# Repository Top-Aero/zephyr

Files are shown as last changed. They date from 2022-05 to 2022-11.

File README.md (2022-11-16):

# Zéphyr

forthebadge  

---

## Description

Le vent d'Ouest, fils d'Astreos et d'Éos, attise le feu de notre inspiration : Zéphyr. Projet phare de l'association [Top Aéro](https://www.top-aero.com/), il s'agit d'une fusée expérimentale transsonique dont la coiffe est équipée de capteurs de pression, afin d'observer l'écoulement de l'air qui l'entoure, puis d'en comparer les résultats à une simulation numérique faite préalablement.

Le dépôt Git contient les conceptions des PCB du système électronique et les codes des microcontrôleurs contenus dans la case électronique de la fusée. Ils sont respectivement contenus dans `case_elec` et `code`.

### Structure du dossier `case_elec`

```
case_elec
├───odb
│   └───odb-backups
├───ressources
└───seq
    └───seq-backups
```

Les sous-dossiers odb et seq, désignant respectivement l'ordinateur de bord et le séquenceur embarqués dans la fusée, contiennent des projets KiCAD, le logiciel de CAO pour l'électronique qui a été utilisé durant la phase de conception. Les fichiers de conception, d'extension kicad_pro, kicad_sch et kicad_pcb suffisent à décrire ce qui a été conçu, mais le fichier .gitignore que nous avions rédigé (il sert à filtrer les documents inutiles dans le workflow Git) a été insuffisant. Avec le temps et le ménage qui n'est pas fait, des documents supplémentaires finissent par encombrer les dossiers KiCAD. Il est tout de même intéressant de les décrire :

- les `*.gbr` sont les fichiers de fabrication, générés par le logiciel ;
- les `*.step` sont les fichiers de visualisation 3D de la carte électronique et des composants ;
- les dossiers `*-backups` contiennent les versions précédentes au format zip d'un même projet.

Les -backups se sont avérés vitaux à une ou deux reprises lorsque nous supprimions des éléments critiques par inadvertance. Bien qu'inutiles en soi, ils compensaient le manque de maîtrise que l'on avait de Git et de KiCAD et faisaient gagner beaucoup de temps. À l'avenir, il faudra penser à configurer KiCAD pour ne conserver que la dernière version, car c'est la plus utile en cas de pépin.

#### Structure du dossier `ressources`

```
ressources
├───3Dmodels
│   └───teensy
├───lib_fp
│   ├───Adafruit BNO055
│   │   ├───Adafruit BNO055-backups
│   │   └───Adafruit BNO055.pretty
│   ├───Adafruit Ultimate GPS
│   │   └───Adafruit Ultimate GPS-backups
│   ├───Adafruit_sensors.pretty
│   ├───Adafruit_Ultimate_GPS
│   │   ├───Adafruit_Ultimate_GPS-backups
│   │   └───Adafruit_Ultimate_GPS.pretty
│   ├───common_misc.pretty
│   ├───MPL3115A2_v0.2
│   │   ├───MPL3115A2_v0.2-backups
│   │   └───MPL3115A2_v0.2.pretty
│   ├───Reyax.pretty
│   └───teensy.pretty
├───lib_sch
└───tmp_resources
    ├───Adafruit-BNO055-Breakout-PCB-master
    │   └───assets
    ├───Adafruit-MPL3115A2-PCB-master
    │   └───assets
    ├───prj
    │   └───altimetre
    └───zip
```

Le dossier ressources se structure ainsi :

- 3Dmodels : contient les modèles 3D des composants. Utile pour la visualisation et l'export au format .step ;
- lib_fp : *library footprints*, contient les empreintes des composants utilisés, c'est-à-dire leur contour et les trous à placer sur la carte électronique ;
- lib_sch : *library schematics*, contient les symboles électriques utilisés dans les schémas électriques ;
- liensUtiles.txt : contient des liens vers des bibliothèques d'empreintes, de symboles électriques et de modèles 3D.
- tmp_ressources : un dossier un peu fouillis qu'il faudrait prendre le temps de réhabiliter.

Le fichier liensUtiles.txt porte mal son nom, car les sites vers lesquels il renvoie se sont avéré moins utiles qu'espérés : des composants complexes comme les capteurs Adafruit n'y sont pas documentés. Il a fallu, et il a mieux valu concevoir par nous même les empreintes, même approximativement. Par ailleurs, Adafruit met à disposition des modèles 3D de leurs composants sur [cette page GitHub](https://github.com/adafruit/Adafruit_CAD_Parts). Toutes les entreprises n'en font pas autant.

### Structure du dossier `code`

```
code
├───seq
├───station-sol
└───telemetrie
    ├───TopAeroEM
    ├───TopAeroEM0720
    ├───TopAeroEM_test_pitot
    └───TopAeroRV
```

Les dossiers seq, TopAEroEM (EM pour émission) et TopAéroRV (RV pour récéption...) dans telemetrie contiennent des fichiers ino. C'est le format de fichier que reconnaît l'éditeur Arduino que l'on utilisait pour programmer les microcontrôleurs de la case électronique. Pour plusieurs raisons, il faut lui préférer à l'avenir son alternative PlatfomIO soit en tant qu'extension, soit en standalone à intégrer au workflow de votre IDE de choix. Pour les experts, un makefile Arduino peut suffire.

Plusieurs dossiers TopAeroEM se côtoient. Une convention de nommage récurrente est de suffixer à une autre version d'un même dossier le mois puis le jour où cette version a vu le jour, en quatre chiffres. Ainsi, le dossier TopAeroEM0720 est une version de TopAeroEM créée un 20 juillet. Des exceptions subsistent (TopAeroEM_test_pitot), mais tant qu'elles ne sont pas nombreuses (plus que 2), elles restent gérables. Ces deux pratiques sont tout de même à éviter, car elles ne tirent pas profit de la technologie de versionnage de Git. Il faut préférer mettre à jour le code existant, ou encore ajouter une nouvelle branche au projet, ou dans le pire des cas, se passer complètement du workflow Git si le contraire amenait à désorganiser la structure du projet.

Le dossier station-sol contient plusieurs scripts qui n'ont pas pu être déployés. Le seul script utilisable en l'état est simpleUSBlogger.py qui se charge d'écrire dans un fichier les données réceptionnées.

## Derniers mots

La fusée a décollé un jour de juillet 2022. À part quelque modifications mineures et sporadiques sur sa page GitHub, le projet est terminé.

## Contacts

Nom               | Rôle                              | Contact
------------------|-----------------------------------|----------
Mohamed-Iadh Bani | Conception séquenceur             | [:e-mail:](mailto:mohamed-iadh.bani@top-aero.com) [:octocat:](https://github.com/mediadhBani)
Théo Tugayé       | Conception ordinateur de bord     | [:e-mail:](mailto:theo.tugaye@top-aero.com) [:octocat:](https://github.com/Alhucarr)

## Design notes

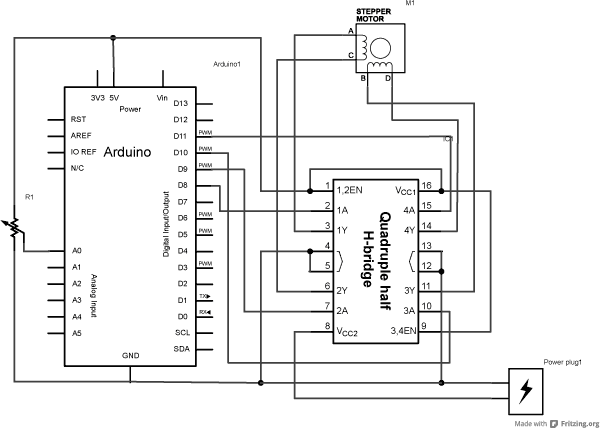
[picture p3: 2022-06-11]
code/stepper/schema_stepper+quadrupleDemiPontH.png

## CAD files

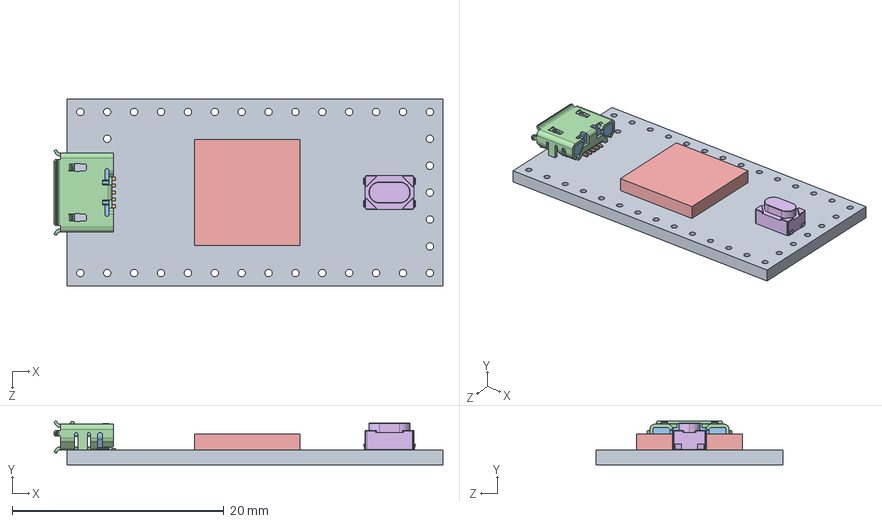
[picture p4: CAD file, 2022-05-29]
case_elec/ressources/3Dmodels/teensy/Teensy_4.0_Assembly.STEP
36.8 x 4.12 x 17.7 mm
Teensy_4.0_PCB
Micro USB-B Female 5Pin SMD
NXP iMXRT1062
SKRPACE010 v4

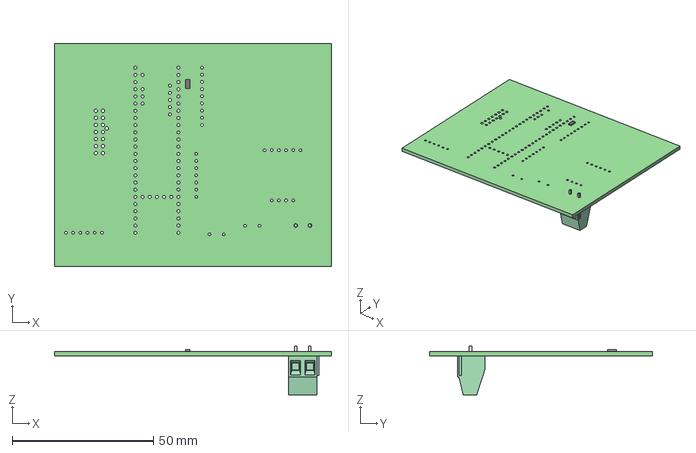
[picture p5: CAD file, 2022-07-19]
case_elec/odb/odb.step
98.0 x 79.0 x 17.3 mm
odb PCB

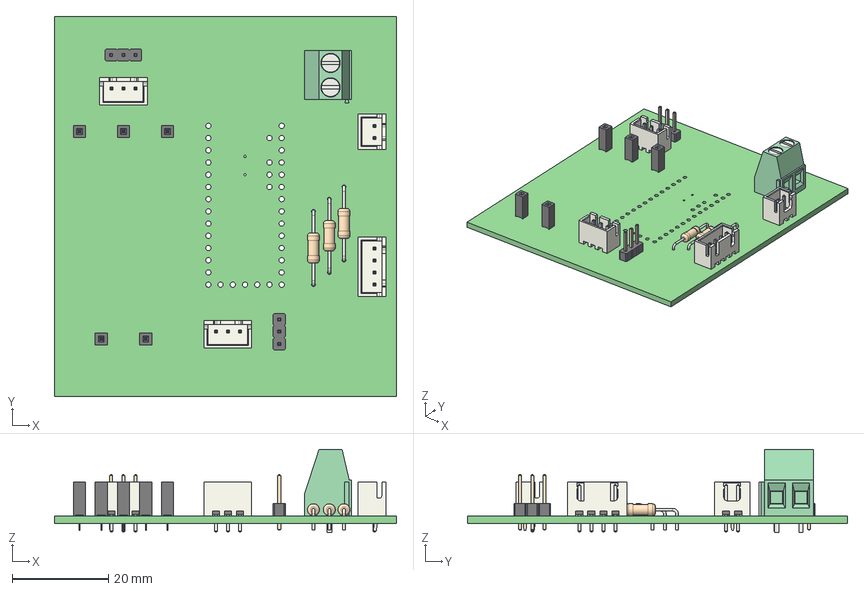
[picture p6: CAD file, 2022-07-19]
case_elec/seq/seq.step
71.1 x 79.0 x 17.3 mm
_autosave-seq PCB

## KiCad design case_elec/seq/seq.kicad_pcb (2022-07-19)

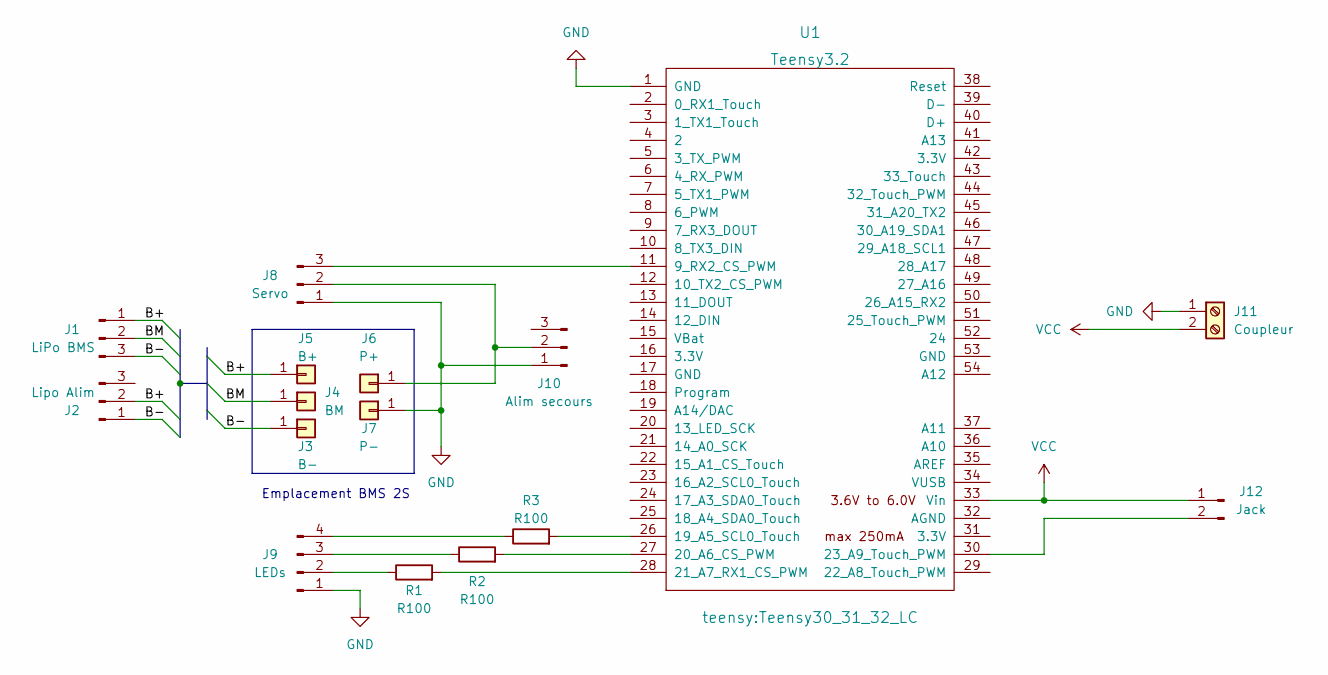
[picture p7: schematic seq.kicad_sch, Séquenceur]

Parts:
J1: LiPo BMS; JST_XH_B3B-XH-A_1x03_P2.50mm_Vertical
J2: Lipo Alim; PinHeader_1x03_P2.54mm_Vertical
J3: B+; PinSocket_1x01_P2.54mm_Vertical
J4: BM; PinSocket_1x01_P2.54mm_Vertical
J5: B-; PinSocket_1x01_P2.54mm_Vertical
J6: P+; PinSocket_1x01_P2.54mm_Vertical
J7: P-; PinSocket_1x01_P2.54mm_Vertical
J8: Servo; JST_XH_B3B-XH-A_1x03_P2.50mm_Vertical
J9: LEDs; JST_XH_B4B-XH-A_1x04_P2.50mm_Vertical
J10: Alim secours; PinHeader_1x03_P2.54mm_Vertical
J11: Coupleur; TerminalBlock_Phoenix_MKDS-1,5-2-5.08_1x02_P5.08mm_Horizont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
J12: Jack; JST_XH_B2B-XH-A_1x02_P2.50mm_Vertical
R1, R2, R3: R100; R_Axial_DIN0207_L6.3mm_D2.5mm_P15.24mm_Horizontal
U1: Teensy3.2; Teensy30_31_32_LC

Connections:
/B+: J1.1, J2.2, J3.1
/B-: J1.3, J2.1, J5.1
/BM: J1.2, J4.1
GND: J7.1, J8.1, J9.1, J10.1, J11.1, U1.1 (GND)
unnamed: J8.3, U1.11 (9_RX2_CS_PWM)
unnamed: J9.2, R1.1
unnamed: J9.3, R2.1
unnamed: J9.4, R3.1
unnamed: J6.1, J8.2, J10.2
unnamed: J12.2, U1.30 (23_A9_Touch_PWM)
unnamed: R1.2, U1.28 (21_A7_RX1_CS_PWM)
unnamed: R2.2, U1.27 (20_A6_CS_PWM)
unnamed: R3.2, U1.26 (19_A5_SCL0_Touch)
VCC: J11.2, J12.1, U1.33 (Vin)

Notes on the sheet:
Emplacement BMS 2S

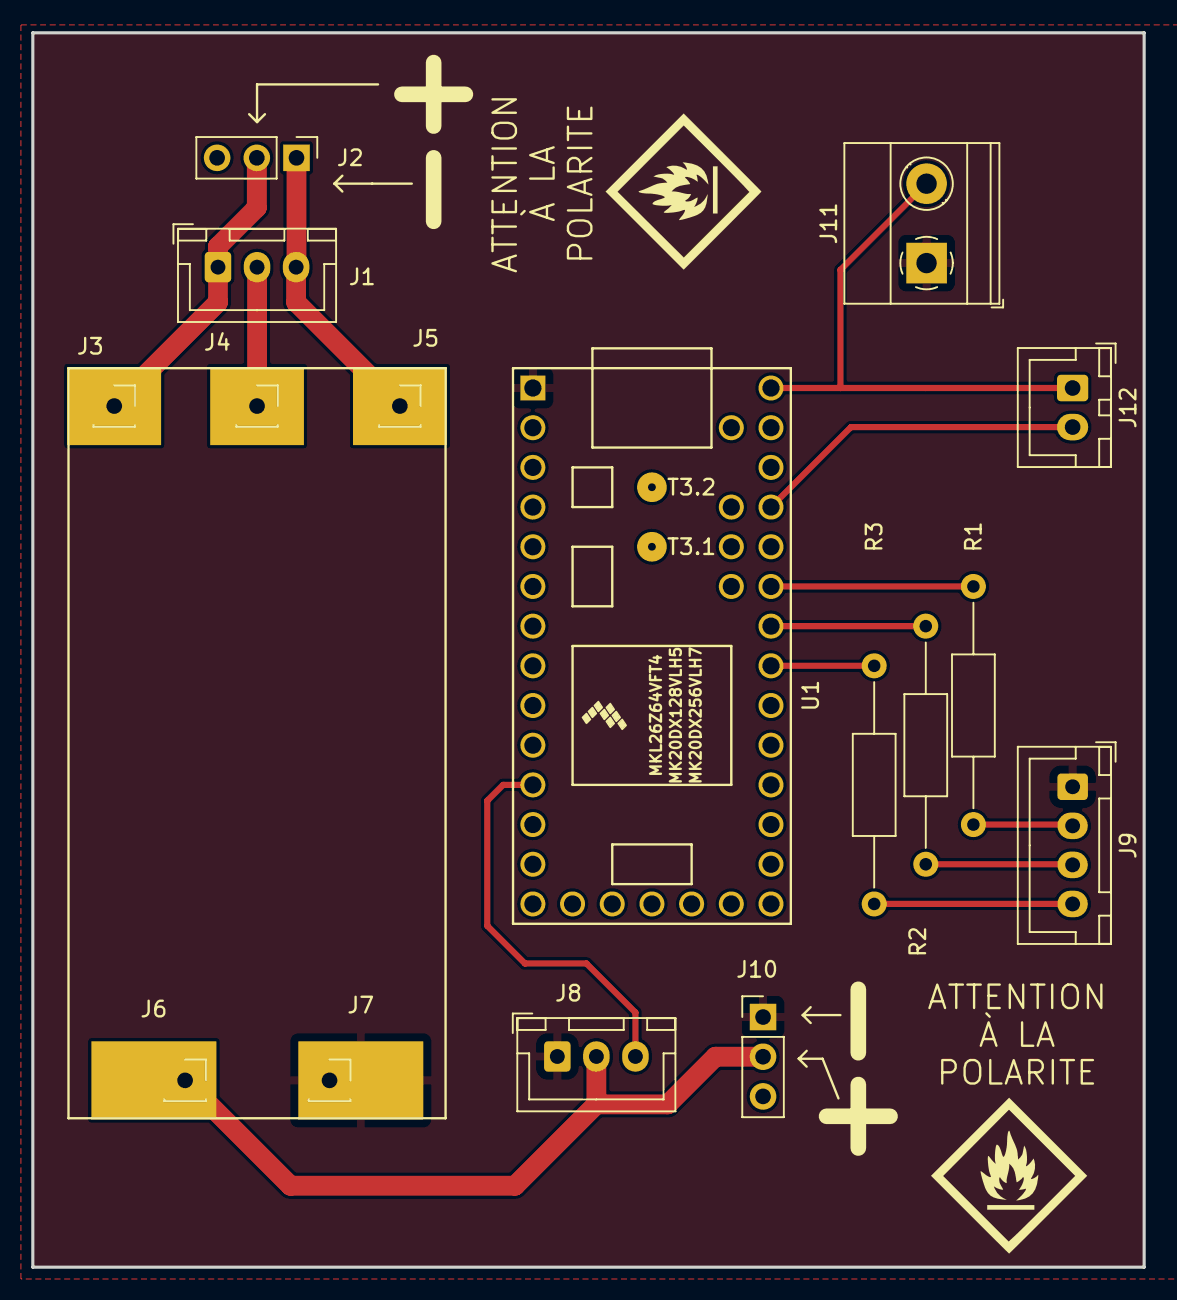
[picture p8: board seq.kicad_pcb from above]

Board: 2 copper layers, 71.1 x 79.0 mm, 16 parts (0 on the bottom side), 14 nets.

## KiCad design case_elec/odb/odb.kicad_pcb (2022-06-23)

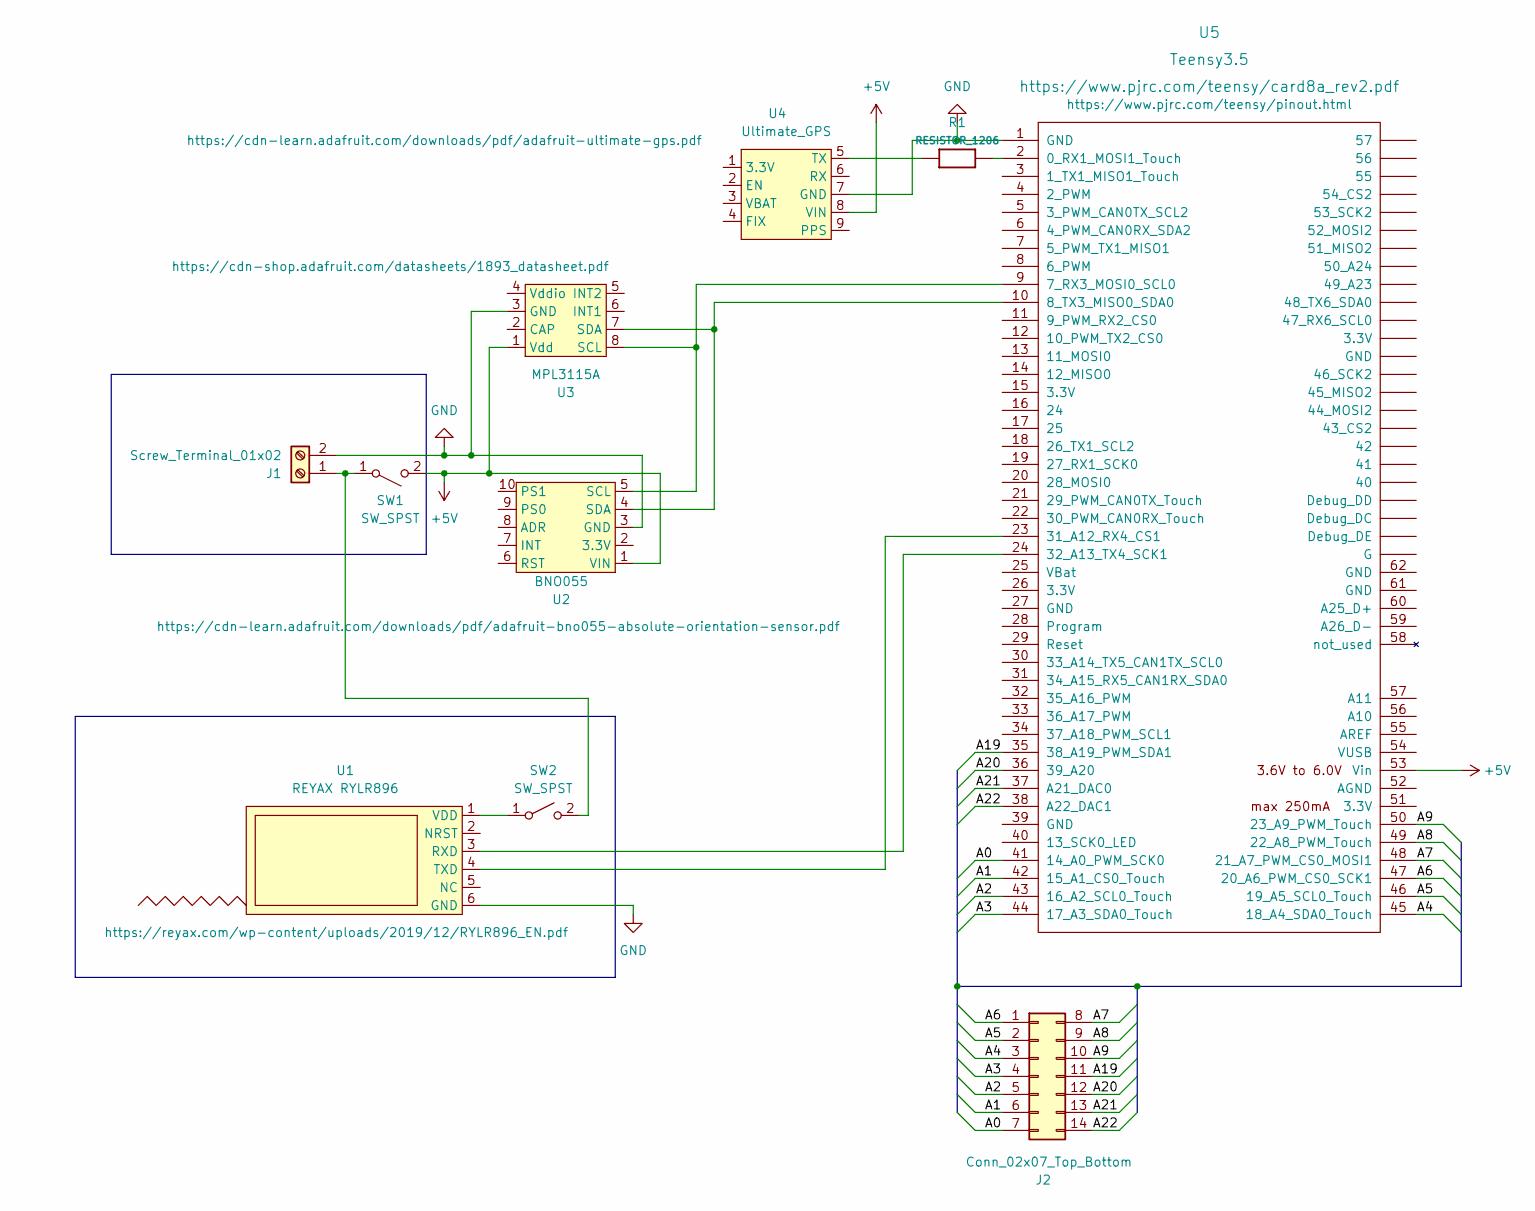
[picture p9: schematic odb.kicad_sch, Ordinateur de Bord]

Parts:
J1: Screw_Terminal_01x02; TerminalBlock_Phoenix_MKDS-1,5-2-5.08_1x02_P5.08mm_Horizont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
J2: Conn_02x07_Top_Bottom; Molex_Nano-Fit_105310-xx14_2x07_P2.50mm_Vertical
R1: RESISTOR_1206; R_1206_3216Metric_Pad1.30x1.75mm_HandSolder
SW1, SW2: SW_SPST; SW
U1: REYAX RYLR896; RYLR896
U2: BNO055
U3: MPL3115A; MPL3115A2
U4: Ultimate_GPS
U5: Teensy3.5; Teensy35_36

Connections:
+5V: SW1.2 (B), U2.1 (VIN), U3.1 (Vdd), U4.8 (VIN), U5.53 (Vin)
/A0: J2.7, U5.41 (14_A0_PWM_SCK0)
/A1: J2.6, U5.42 (15_A1_CS0_Touch)
/A2: J2.5, U5.43 (16_A2_SCL0_Touch)
/A3: J2.4, U5.44 (17_A3_SDA0_Touch)
/A4: J2.3, U5.45 (18_A4_SDA0_Touch)
/A5: J2.2, U5.46 (19_A5_SCL0_Touch)
/A6: J2.1, U5.47 (20_A6_PWM_CS0_SCK1)
/A7: J2.8, U5.48 (21_A7_PWM_CS0_MOSI1)
/A8: J2.9, U5.49 (22_A8_PWM_Touch)
/A9: J2.10, U5.50 (23_A9_PWM_Touch)
/A19: J2.11, U5.35 (38_A19_PWM_SDA1)
/A20: J2.12, U5.36 (39_A20)
/A21: J2.13, U5.37 (A21_DAC0)
/A22: J2.14, U5.38 (A22_DAC1)
GND: J1.2, U1.6 (GND), U2.3 (GND), U3.3 (GND), U4.7 (GND), U5.1 (GND)
unnamed: J1.1, SW1.1 (A), SW2.2 (B)
unnamed: SW2.1 (A), U1.1 (VDD)
unnamed: U1.3 (RXD), U5.24 (32_A13_TX4_SCK1)
unnamed: U1.4 (TXD), U5.23 (31_A12_RX4_CS1)
unnamed: U2.4 (SDA), U3.7 (SDA), U5.10 (8_TX3_MISO0_SDA0)
unnamed: U2.5 (SCL), U3.8 (SCL), U5.9 (7_RX3_MOSI0_SCL0)
unnamed: R1.1, U4.5 (TX)
unnamed: R1.2, U5.2 (0_RX1_MOSI1_Touch)

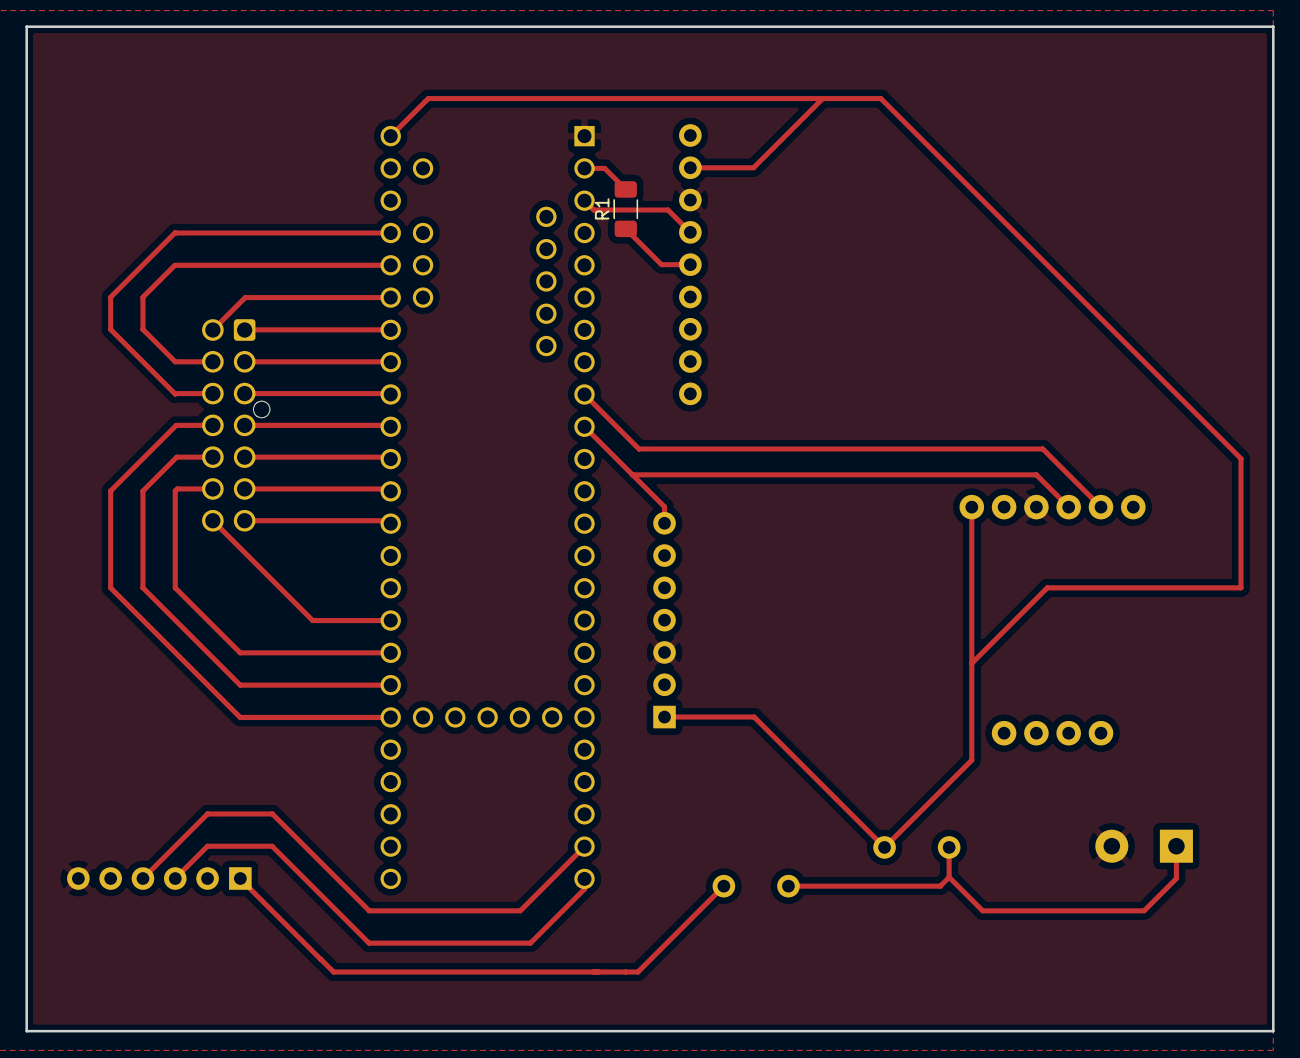
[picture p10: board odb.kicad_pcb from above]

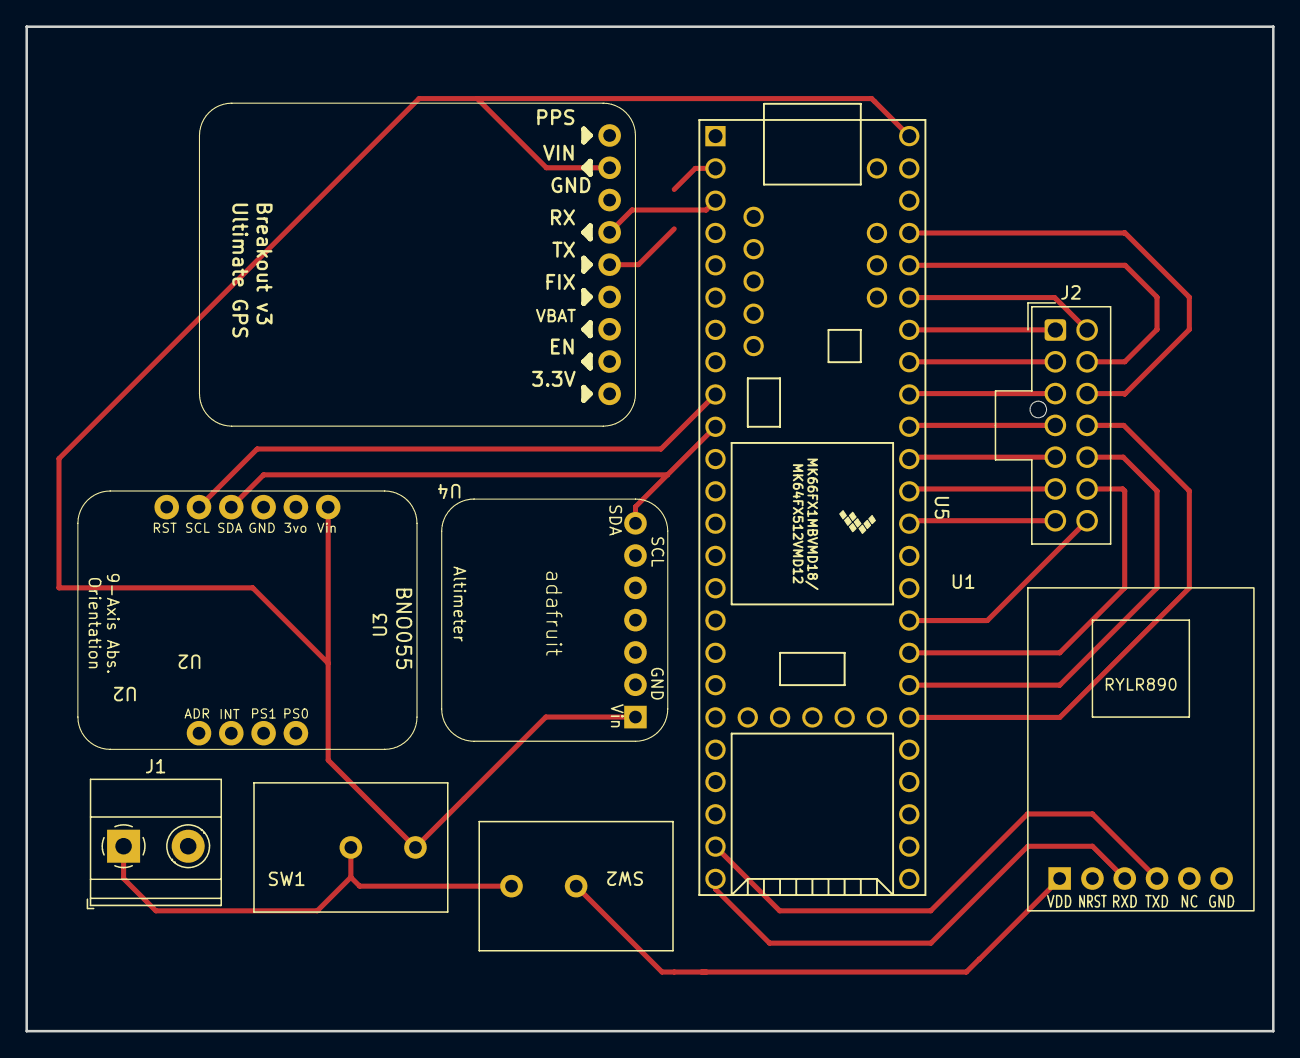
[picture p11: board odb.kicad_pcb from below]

Board: 2 copper layers, 98.0 x 79.0 mm, 10 parts (9 on the bottom side), 24 nets.

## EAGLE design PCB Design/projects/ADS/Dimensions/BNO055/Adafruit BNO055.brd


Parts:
C1, C2: 22pF; 0805-NO
C3: 0.1uF; 0805-NO
C4: 0.1uF; 0805_10MGAP
C5: 10uF; 0805-NO
C6: 10uF; 0805_10MGAP
D1: 1n4148; SOD-323
FID1, FID2: FIDUCIAL""; FIDUCIAL_1MM
JP1: HEADER-1X676MIL; 1X06_ROUND_76
JP2: HEADER-1X476MIL; 1X04_ROUND_76
Q1, Q2: BSS138; SOT23-WIDE
R3, R4, R5, R6, R7, R10: 10K; 0805-NO
R8, R9: 10K; _0805MP
U1: MIC5225-3.3; SOT23-5
U$2: BNO055
U$29, U$30, U$31, U$32: MOUNTINGHOLE2.5_THICK; MOUNTINGHOLE_2.5_PLATED_THICK
Y1: 32.768kHz; CRYSTAL_8X3.8

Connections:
3.3V: C4.2, C6.1, JP1.2, Q1.1 (G), Q2.1 (G), R6.2, R7.2, R10.2, U1.5 (OUT), U$2.3 (VDD), U$2.4 (NBOOT_LOAD_PIN), U$2.28 (VDDIO)
5.0V: C5.1, JP1.1, R8.2, R9.2, U1.1 (IN), U1.3 (EN)
GND: C1.1, C2.1, C3.1, C4.1, C5.2, C6.2, JP1.3, R3.2, R4.2, R5.2, U1.2 (GND), U$2.2 (GND), U$2.10 (PIN10(GND)), U$2.15 (PIN15(GND)), U$2.16 (PIN16(GND)), U$2.18 (COM2(GND)), U$2.25 (GND)
I2CADDR_3V: JP2.4, R5.1, U$2.17 (COM3/I2C_ADDR)
INT_3V: JP2.3, U$2.14 (INT)
unnamed: C1.2, U$2.27 (XIN32), Y1.P$4 (2)
unnamed: C2.2, U$2.26 (XOUT32), Y1.P$1 (1)
unnamed: C3.2, U$2.9 (CAP)
NRESET_3V: D1.A, R10.1, U$2.11 (NRESET)
PS0_3V: JP2.1, R3.1, U$2.6 (PS0)
PS1_3V: JP2.2, R4.1, U$2.5 (PS1)
RST_5V: D1.C, JP1.6
SCL_3V: Q2.2 (S), R7.1, U$2.19 (COM1/SCL/RX)
SCL_5V: JP1.5, Q2.3 (D), R9.1
SDA_3V: Q1.2 (S), R6.1, U$2.20 (COM0/SDA/TX)
SDA_5V: JP1.4, Q1.3 (D), R8.1



Board: 2 copper layers, 26.7 x 20.3 mm, 31 parts (2 on the bottom side), 16 nets.

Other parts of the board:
U$3: PCBFEAT-REV-040
U$28: ADAFRUIT_TEXT_20MM
U$33: ADAFRUIT_2.5MM

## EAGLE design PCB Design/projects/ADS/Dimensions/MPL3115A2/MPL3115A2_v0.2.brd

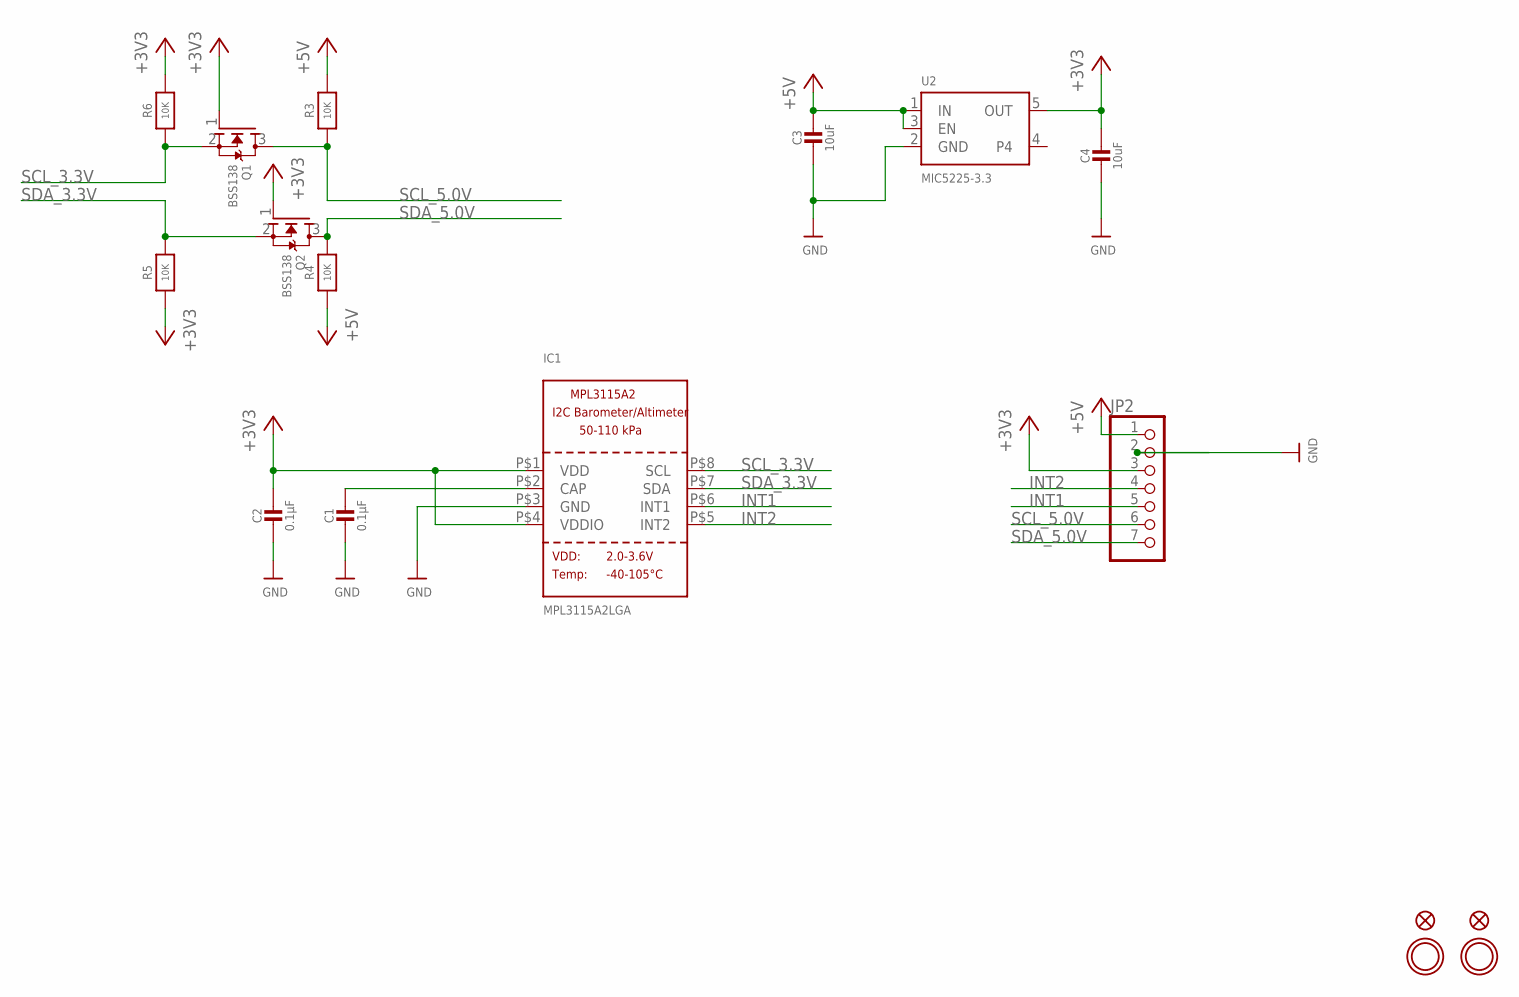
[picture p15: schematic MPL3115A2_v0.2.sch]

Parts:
C1, C2: 0.1µF; 0805-NO
C3, C4: 10uF; 0805-NO
FID1, FID2: FIDUCIAL""; FIDUCIAL_1MM
IC1: MPL3115A2LGA; LGA8
JP2: HEADER-1X770MIL; 1X07_ROUND_70
Q1, Q2: BSS138; SOT23-WIDE
R3, R4, R5, R6: 10K; 0805-NO
U2: MIC5225-3.3; SOT23-5
U$8, U$9: MOUNTINGHOLE2.5; MOUNTINGHOLE_2.5_PLATED

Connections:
+3V3: C2.1, C4.1, IC1.P$1 (VDD), IC1.P$4 (VDDIO), JP2.3, Q1.1 (G), Q2.1 (G), R5.1, R6.2, U2.5 (OUT)
+5V: C3.1, JP2.1, R3.2, R4.1, U2.1 (IN), U2.3 (EN)
CAP: C1.1, IC1.P$2 (CAP)
GND: C1.2, C2.2, C3.2, C4.2, IC1.P$3 (GND), JP2.2, U2.2 (GND)
INT1: IC1.P$6 (INT1), JP2.5
INT2: IC1.P$5 (INT2), JP2.4
SCL_3.3V: IC1.P$8 (SCL), Q1.2 (S), R6.1
SCL_5.0V: JP2.6, Q1.3 (D), R3.1
SDA_3.3V: IC1.P$7 (SDA), Q2.2 (S), R5.2
SDA_5.0V: JP2.7, Q2.3 (D), R4.2

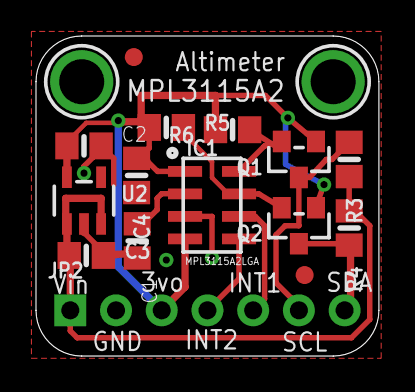
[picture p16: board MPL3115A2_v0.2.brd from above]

Board: 2 copper layers, 19.1 x 17.8 mm, 18 parts (1 on the bottom side), 10 nets.

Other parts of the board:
U$14: ADAFRUIT_3.5MM

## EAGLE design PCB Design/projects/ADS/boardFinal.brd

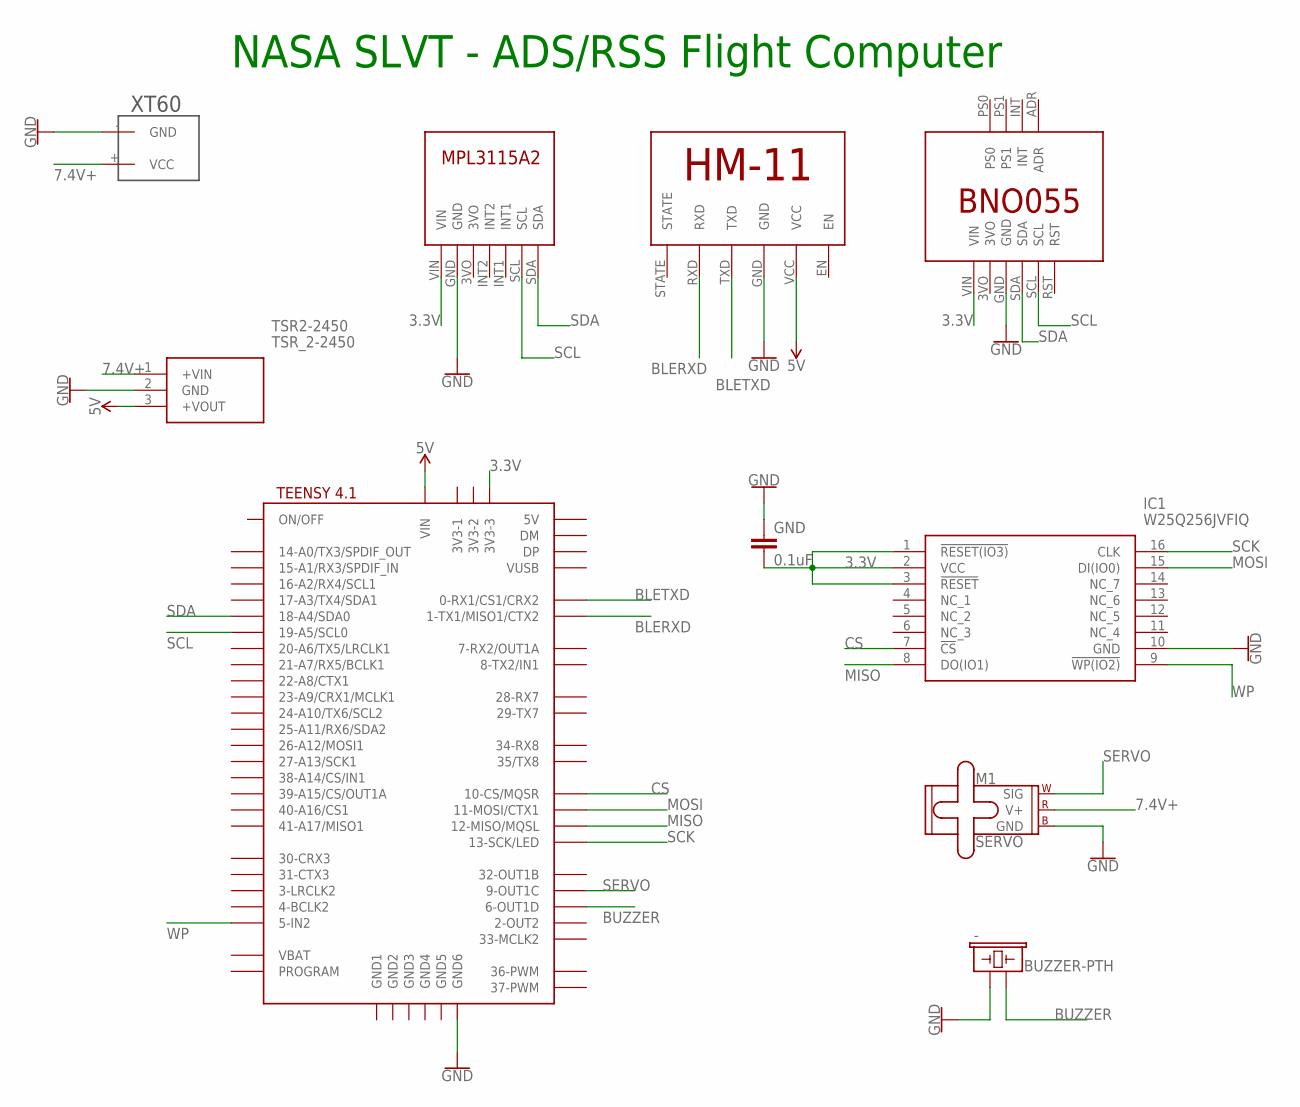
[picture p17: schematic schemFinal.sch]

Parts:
-: BUZZER-PTH; BUZZER-12MM
GND: 0.1uF; CAP-PTH-2.54
IC1: W25Q256JVFIQ; SOIC127P1032X264-16N
M1: SERVO; 1X03
TSR2-2450: TSR_2-2450; TSR-2
U$1: BNO055
U$2: MPL3115A2
U$3: TEENSY41-E; TENNSY41-E
U$4: HM-11
U$5: XT60

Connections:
3.3V: GND.2, IC1.1 (!RESET(IO3)), IC1.2 (VCC), IC1.3 (!RESET), U$1.VIN, U$2.VIN, U$3.3V3-3
5V: TSR2-2450.3 (+VOUT), U$3.VIN, U$4.VCC
7.4V+: M1.2 (V+), TSR2-2450.1 (+VIN), U$5.+ (VCC)
BLERXD: U$3.1-TX1/MISO1/CTX2, U$4.RXD
BLETXD: U$3.0-RX1/CS1/CRX2, U$4.TXD
BUZZER: -.- (2), U$3.6-OUT1D
CS: IC1.7 (!CS), U$3.10-CS\MQSR (10-CS/MQSR)
GND: -.+ (1), GND.1, IC1.10 (GND), M1.3 (GND), TSR2-2450.2 (GND), U$1.GND, U$2.GND, U$3.GND6, U$4.GND, U$5.- (GND)
MISO: IC1.8 (DO(IO1)), U$3.12-MISO/MQSL
MOSI: IC1.15 (DI(IO0)), U$3.11-MOSI/CTX1
SCK: IC1.16 (CLK), U$3.13-SCK/LED
SCL: U$1.SCL, U$2.SCL, U$3.19-A5/SCL0
SDA: U$1.SDA, U$2.SDA, U$3.18-A4/SDA0
SERVO: M1.1 (SIG), U$3.9-OUT1C
WP: IC1.9 (!WP(IO2)), U$3.5-IN2

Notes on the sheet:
NASA SLVT - ADS/RSS Flight Computer

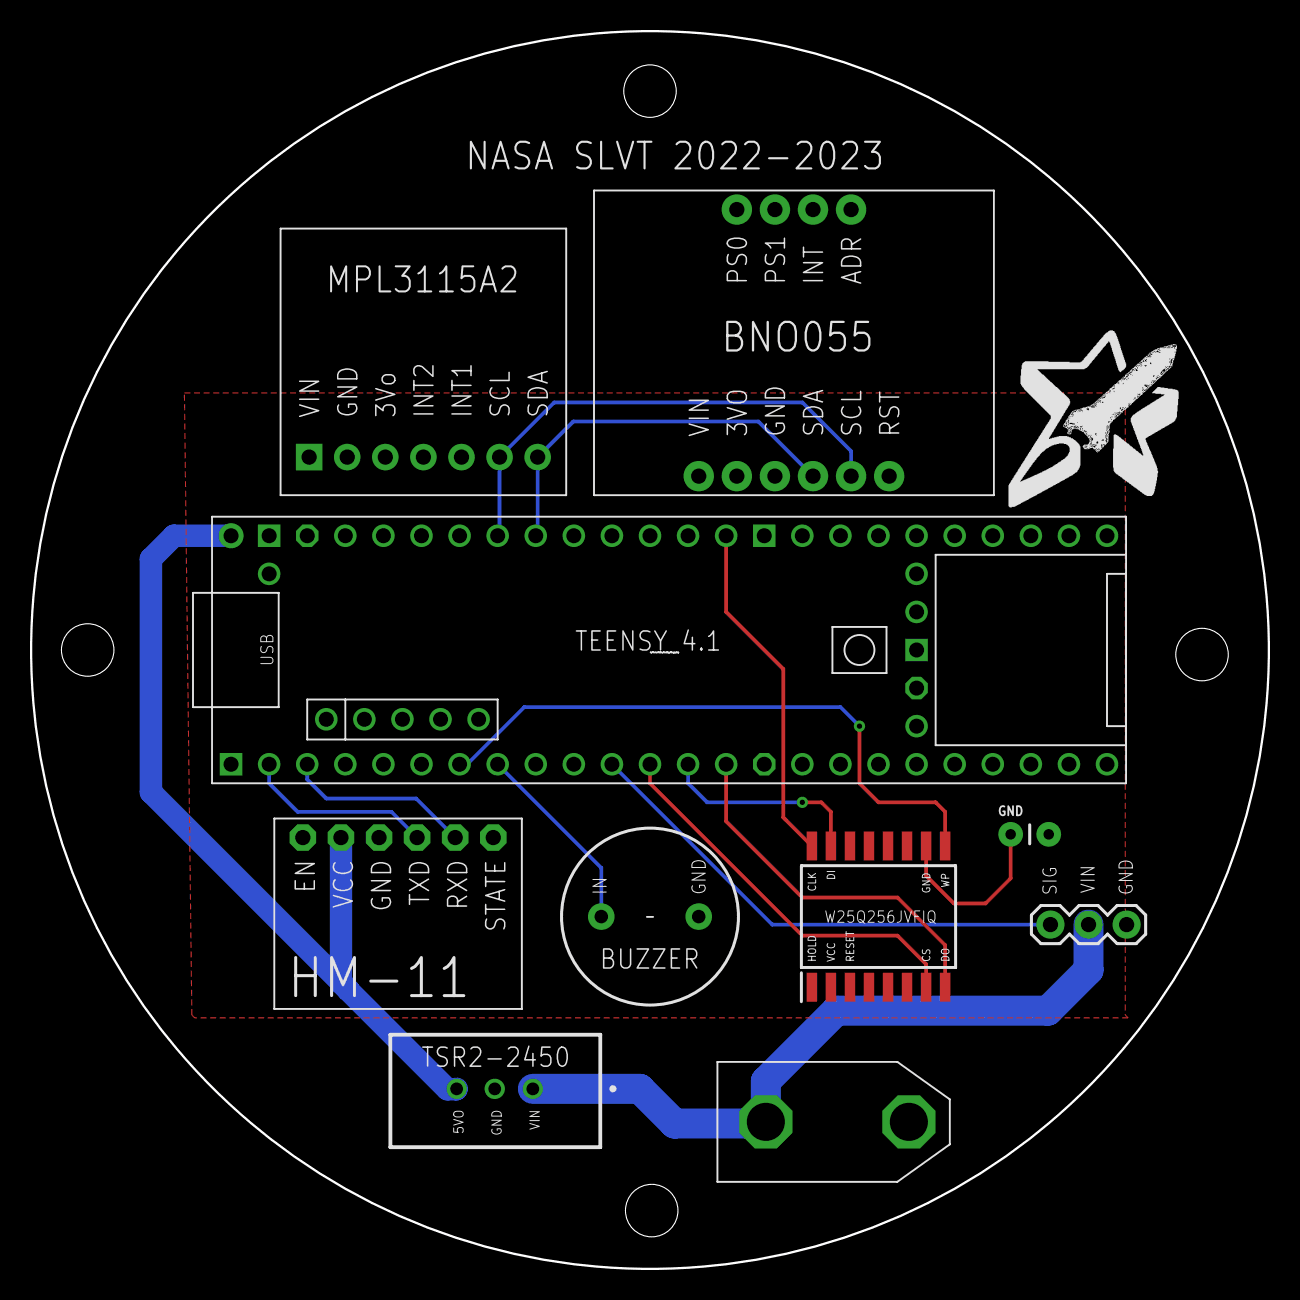
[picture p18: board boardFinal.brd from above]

Board: 2 copper layers, 82.5 x 82.5 mm, 10 parts (0 on the bottom side), 15 nets.

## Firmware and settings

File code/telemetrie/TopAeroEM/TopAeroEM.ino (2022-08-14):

/*
  Auteurs: Nicolas Armogathe, Théo TUGAYE, pour l'association TopAero - Sorbonne Université  
  - Mesures d'accélération, altitude, position GPS
  - Transmission radio des données
  - Enregistrement des données sur carte uSD
  projet actuel: Zéphyr
  Libre de droit
  */
  
#define SCB_AIRCR (*(volatile uint32_t *)0xE000ED0C) // Application Interrupt and Reset Control location

#include <Wire.h>
#include <SoftwareSerial.h>

static const int RXPin = 0, TXPin = 1;      /* GPS */
static const uint32_t GPSBaud = 9600;
SoftwareSerial ss(RXPin, TXPin);

#include <Adafruit_Sensor.h>  //librairie Adafruit générale des capteurs 
#include <Adafruit_BNO055.h>  //librairie du module inertiel /* Accélération */
#include <utility/imumaths.h> //librairie pour le fonctionnement du module inertiel 

#include <Adafruit_GPS.h> //librairie Adafruit du module GPS /* GPS */

int ledState=LOW;
unsigned long preMillis=0;

#define BNO055_SAMPLERATE_DELAY_MS (5)        /* Accélération */
Adafruit_BNO055 bno = Adafruit_BNO055(55, 0x28); //by default address is 0x29 or 0x28 /* Accélération */

                      /*Pression*/
float tension1, P1, tension2, P2, tension3, P3, tension4, P4, tension5, P5, tension6, P6, tension7, P7, tension8, P8, tension9, P9, tension10, P10, tension11, P11, tension12, P12, tension13, P13, tension14, P14;//Déclaration des variables tension et pression

bool first=true;      /* Altitude */
float altm0=0.0;
#define ALTMODE //comment out for barometer mode; default is altitude mode 
const int SENSORADDRESS = 0x60; // address specific to the MPL3115A1, value found in datasheet 
float altsmooth = 0; //for exponential smoothing          
byte IICdata[5] = {0,0,0,0,0}; //buffer for sensor data 
float firstalt=0.0;

#define mySerial Serial1      /* GPS */
Adafruit_GPS GPS(&mySerial);
bool firstGPS;

int comdata=0;      /* Radio */
int data_lenght;
String comstr;
char* frame;
SoftwareSerial lora(9,10);

#include <SD.h>       /* uSD */
#include <SPI.h>      
File myFile;
File tableau;
const int chipSelect = BUILTIN_SDCARD;
int i=0; //Compteur du nombre de mesures

// @mib
float tab_acl[3] = {0, 0, 0};

void setup() {
  Wire.begin(); //join i2c bus 
  Wire.setSDA(8); // Activation du mode alternatif du pin
  Wire.setSCL(7); // Activation du mode alternatif du pin     
  Serial.begin(115200);//ouverture port série 1 USB
  pinMode(13,OUTPUT); //LED
  Serial2.begin(115200);//ouverture port série 2 pour radio
  
  ///////////////////////////////////////////////////////////////////////////////////////////////////////
                                                  /* GPS */
                                                  
  GPS.begin(9600); //baudrate obligé du module
  ss.begin(GPSBaud);
  // this line to turn on only the "minimum recommended" data
  GPS.sendCommand(PMTK_SET_NMEA_OUTPUT_RMCONLY);
  // Set the update rate
  GPS.sendCommand(PMTK_SET_NMEA_UPDATE_10HZ); //taux de rafraichissement 10Hz, en réalité il n'est pas représentatif 
  //du rafraichissement réel, mais il vaut mieux entrer la commande tout de même
  
  ///////////////////////////////////////////////////////////////////////////////////////////////////////
                                              /* Accélération */
  /* Initialise the sensor */
 /*  if(!bno.begin())
  {
    Serial.print("Couldnt find accelerator sensor");
    while(1);
  }*/

  bno.setExtCrystalUse(true);
  ///////////////////////////////////////////////////////////////////////////////////////////////////////
                                                /* Altitude */       
  IIC_Write(0x2D,0); //write altitude offset=0 (because calculation below is based on offset=0)
  //Altitude mode
  IIC_Write(0x26, 0b10111011); //bit 2 is one shot mode //0xB9 = 0b10111001
  IIC_Write(0x26, 0b10111001); //must clear oversampling (OST) bit, otherwise update will be once per second
  delay(1000); //wait for measurement
  IIC_ReadData(); //
  firstalt=Alt_Read();
  altsmooth=Alt_Read()-firstalt;
  ///////////////////////////////////////////////////////////////////////////////////////////////////////
                                                 /* Radio */ 
  lora.begin(115200); //baudrate obligé du module
  delay(20);
  lora.println("AT+BAND=869650000\r\n"); //commande pour appliquer la fréquence d'émission ou réception du module
  //ici 869,65Mhz
  delay(20);
  lora.println("AT+PARAMETER=7,9,4,4\r\n"); //par défaut = 12,7,1,4 
  //Spreading factor = 7, Bandwidth = 9 (500kHz), Coding rate = 4, Programmed Preamble = 4
  delay(2000);
  Serial.println("Communication prête");
  ///////////////////////////////////////////////////////////////////////////////////////////////////////
                                                 /* uSD */
  Serial.print("Initializing SD card...");
  if (!SD.begin(chipSelect)) {
    Serial.println("initialization failed!");
    return;
  }
  Serial.println("initialization done.");
  myFile = SD.open("zephyr.txt", FILE_WRITE);
  if (myFile) {
    myFile.println("Zephyr_new_stream");
    myFile.close();
  } else {
    Serial.println("error opening zephyr.txt");
  }

    /* Ouvre le fichier csv en écriture */
  Serial.println(F("Ouverture du fichier csv ... "));
  tableau = SD.open("zephyr.csv", FILE_WRITE);
  if (!tableau) {
    Serial.println(F("Erreur : Impossible d'ouvrir le fichier de sortie"));
    Serial.println(F("Verifiez la carte SD et appuyez sur le bouton RESET"));
    for (;;); // Attend appui sur bouton RESET
  }
  /* Ajoute l'entête CSV si le fichier est vide */
  if (tableau.size() == 0) {
    Serial.println(F("Ecriture de l'entete CSV ..."));
    tableau.flush();
  }
  delay(2000);
}//fin setup



uint32_t timer = millis();

bool alt_must_adjust = true; //condition pour ajuster l'altitude au bout de 1min

void loop() {
 
  String framestr;

  ///////////////////////////////////////////////////////////////////////////////////////////////////////
                                      /*Pression*/

  tension2 = analogRead(A16) * 5.0 / 1023.0;
  P2 = (tension2 / 0.002 - 39.75);
  Serial.println("P2 :");
  Serial.print(P2, 0);
  Serial.println(" hPa");
  
  tension4 = analogRead(A18) * 5.0 / 1023.0;
  P4 = (tension4 / 0.002 - 34.75);
  Serial.println("P4 :");
  Serial.print(P4, 0);
  Serial.println(" hPa");
  
  tension5 = analogRead(A14) * 5.0 / 1023.0;
  P5 = (tension5 / 0.002 - 48.75);
  Serial.println("P5 :");
  Serial.print(P5, 0);
  Serial.println(" hPa");
  
  tension6 = analogRead(A15) * 5.0 / 1023.0;
  P6 = (tension6 / 0.002 - 44.75);
  Serial.println("P6 :");
  Serial.print(P6, 0);
  Serial.println(" hPa");
  
  tension7 = analogRead(A17) * 5.0 / 1023.0;
  P7 = (tension7 / 0.002 - 39.75);
  Serial.println("P7 :");
  Serial.print(P7, 0);
  Serial.println(" hPa");
  
  tension8 = analogRead(A9) * 5.0 / 1023.0;
  P8 = (tension8 / 0.002 - 53.75);
  Serial.println("P8 :");
  Serial.print(P8, 0);
  Serial.println(" hPa");
  
  tension9 = analogRead(A8) * 5.0 / 1023.0;
  P9 = (tension9 / 0.002 - 24.75);
  Serial.println("P9 :");
  Serial.print(P9, 0);
  Serial.println(" hPa");
  
  tension10 = analogRead(A7) * 5.0 / 1023.0;
  P10 = (tension10 / 0.002 - 29.75);
  Serial.println("P10 :");
  Serial.print(P10, 0);
  Serial.println(" hPa");
  
  tension11 = analogRead(A6) * 5.0 / 1023.0;
  P11 = (tension11 / 0.002 - 31.75);
  Serial.println("P11 :");
  Serial.print(P11, 0);
  Serial.println(" hPa");
  
  tension12 = analogRead(A3) * 5.0 / 1023.0;
  P12 = (tension12 / 0.002 - 36.75);
  Serial.println("P12 :");
  Serial.print(P12, 0);
  Serial.println(" hPa");

  tension13 = analogRead(A2) * 5.0 / 1023.0;
  P13 = (tension13 / 0.002 - 53.75);
  Serial.println("P13 :");
  Serial.print(P13, 0);
  Serial.println(" hPa");

  tension14 = analogRead(A1) * 5.0 / 1023.0;//Lecture de la tension et conversion en V
  P14 = (tension14 / 0.002 - 49.75); //Obtention de la pression en hPa => valeur 93 = offset , a changer pour chaque capteur 
  //Affichage de la pression sur le3moniteur série
  Serial.println("P14 :");
  Serial.print(P14, 0);
  Serial.println(" hPa");
  
  ///////////////////////////////////////////////////////////////////////////////////////////////////////  
                                                      /* GPS */
  firstGPS=true;
  while (ss.available() > 0){
  GPS.read();
  char* frame = GPS.lastNMEA();
  GPS.parse(frame);
    if(firstGPS){
      Serial.println(frame);
      firstGPS=not(firstGPS);
      framestr=String(frame);
   
    }
  }
  
  ///////////////////////////////////////////////////////////////////////////////////////////////////////
  unsigned long ms = millis();                     /* LED blink */
  if((ms-preMillis)>=250){
    preMillis=ms;
    if(ledState==LOW){
      ledState=HIGH;
    }
    else{
      ledState=LOW;
    }
    digitalWrite(13,ledState);
  }
  
  ///////////////////////////////////////////////////////////////////////////////////////////////////////
                                              /* Accélération (m/s^2) */
  // mib note : plus besoin a compter du 2021-07-20.
  //Serial.print(accelModule);
  //Serial.println("");
  ///////////////////////////////////////////////////////////////////////////////////////////////////////
                                                  /* Altitude (m) */ 
  float altitudeSmoothed=altitude_read_data()-altm0;//soustraire altm0 pour commencer à l'altitude 0
  if(first==true){                            // +/- 1m de précision
    if(ms>60000){ //on attend 1min pour avoir une valeur stable d'altitude
      altm0=altitudeSmoothed;
      first=false;
    }
  }
  
  Serial.print(ms);
  Serial.println("");
  
  ///////////////////////////////////////////////////////////////////////////////////////////////////////
                                                  /* Radio */
                                                  
  String mes=" alt="+String(altitudeSmoothed)+" acx="+String(tab_acl[0])+" acy="+String(tab_acl[1])+" acz="+String(tab_acl[2])+" tps="+String(millis())+" gps="+framestr;
  
  String datas=mes+" P11="+String(P11)+" P12="+String(P12);
  datas=datas.trim();
  String cmd="AT+SEND=0,"+String(mes.length()) +","+ datas +"\r\n";
  lora.println(cmd);
  while(lora.available()){
    Serial.write(lora.read());
  }
  Serial.println();
  Serial.println(cmd);
  delay(35); //le délai influe sur la transmission radio, si trop court il y a une probabilité +/- importante 
  //que les messages soient coupés

  ///////////////////////////////////////////////////////////////////////////////////////////////////////
                                                      /* uSD */
  myFile = SD.open("zephyr.txt", FILE_WRITE);
  if (myFile) {
    myFile.print("Mesure ");
    myFile.println(i);
    myFile.print("\nTemps = ");
    myFile.println(String(millis()));
    myFile.print("Altitude = ");
    myFile.println(String(altitudeSmoothed));
    myFile.print("Accéleration en X = ");
    myFile.println(String(tab_acl[0]));
    myFile.print("Accéleration en Y = ");
    myFile.println(String(tab_acl[1]));
    myFile.print("Accéleration en Z = ");
    myFile.println(String(tab_acl[2]));
    //myFile.println(String(accelModule));
    myFile.print("Coordonnées GPS = ");
    myFile.println(framestr);
    myFile.print("Pression 2 = "); myFile.println(String(P2));
    myFile.print("Pression 4 = "); myFile.println(String(P4));
    myFile.print("Pression 5 = "); myFile.println(String(P5));
    myFile.print("Pression 6 = "); myFile.println(String(P6));
    myFile.print("Pression 7 = "); myFile.println(String(P7));
    myFile.print("Pression 8 = "); myFile.println(String(P8));
    myFile.print("Pression 9 = "); myFile.println(String(P9));
    myFile.print("Pression 10 = "); myFile.println(String(P10));
    myFile.print("Pression 11 = "); myFile.println(String(P11));
    myFile.print("Pression 12 = "); myFile.println(String(P12));
    myFile.print("Pression 13 = "); myFile.println(String(P13));
    myFile.print("Pression 14 = "); myFile.println(String(P14));
    myFile.print("\n");
    myFile.close();
  }
  tableau = SD.open("zephyr.csv", FILE_WRITE);
  if (tableau) {
    tableau.print(i);
    tableau.print(";"); 
    tableau.print(millis());
    tableau.print(";"); 
    tableau.print(altitudeSmoothed);
    tableau.print(";");
    tableau.print(tab_acl[0]);
    tableau.print(";");
    tableau.print(tab_acl[1]);
    tableau.print(";");
    tableau.print(tab_acl[2]);
    tableau.print(";");
    tableau.print(framestr);
    tableau.print(";");
    tableau.print(P2);
    tableau.print(";");
    tableau.print(P4);
    tableau.print(";");
    tableau.print(P5);
    tableau.print(";");
    tableau.print(P6);
    tableau.print(";");
    tableau.print(P7);
    tableau.print(";");
    tableau.print(P8);
    tableau.print(";");
    tableau.print(P9);
    tableau.print(";");
    tableau.print(P10);
    tableau.print(";");
    tableau.print(P11);
    tableau.print(";");
    tableau.print(P12);
    tableau.print("\n");
    tableau.print(P13);
    tableau.print(";");
    tableau.print(P14);
    tableau.print("\n");
    tableau.close();
  }
  i=i+1;
 delay(200);
}//fin loop

///////////////////////////////////////////////////////////////////////////////////////////////////////
                                                  /* Accélération */
void accel_read_data(float tab_acl[3]){
  /* Get a new sensor event */
  sensors_event_t event;
  bno.getEvent(&event);
  /* Vecteur contenant les composantes des accélérations */
  imu::Vector<3> accelerometer = bno.getVector(Adafruit_BNO055::VECTOR_ACCELEROMETER);

  /*float mod_accel=sqrt(pow(accelerometer.x(),2)+pow(accelerometer.y(),2)+pow(accelerometer.z(),2))-9.80665;
  if (mod_accel<0){
   mod_accel=0;
  }*/
  /*
  Serial.print("Acceleration:");
  Serial.println(accelerometer.x());
  Serial.println(accelerometer.y());
  Serial.println(accelerometer.z());
  delay(BNO055_SAMPLERATE_DELAY_MS);*/

  tab_acl[0] = accelerometer.x();
  tab_acl[1] = accelerometer.y();
  tab_acl[2] = accelerometer.z();
}

/////////////////////////////////////////////////////////////////////////////////////////////////////////
                                                    /* Altitude */
                                      //by Henry Lahr, 2013-02-27, libre de droit
float altitude_read_data(){
  // This function reads the altitude (or barometer) and temperature registers, then prints their values
  // variables for the calculations
  float altbaro;
  //One shot mode at 0b10101011 is slightly too fast, but better than wasting sensor cycles that increase precision
  //one reading seems to take 4ms (datasheet p.33);
  //oversampling at 32x=130ms interval between readings seems to be optimal for 10Hz
  //#ifdef ALTMODE //Altitude mode
    IIC_Write(0x26, 0b10111011); //bit 2 is one shot mode //0xB9 = 0b10111001
    IIC_Write(0x26, 0b10111001); //must clear oversampling (OST) bit, otherwise update will be once per second
  //#else //Barometer mode
    //IIC_Write(0x26, 0b00111011); //bit 2 is one shot mode //0xB9 = 0b10111001
    //IIC_Write(0x26, 0b00111001); //must clear oversampling (OST) bit, otherwise update will be once per second
  //#endif
  //delay(20); //read with 10Hz; drop this if calling from an outer loop
  IIC_ReadData(); //reads registers from the sensor
  #ifdef ALTMODE //converts byte data into float; change function to Alt_Read() or Baro_Read()
    altbaro = Alt_Read()-firstalt;
  #endif
  //altsmooth=(altsmooth*3+altbaro)/4; //exponential smoothing to get a smooth time series, pas bon pour des changements brutaux
  //Serial.print(altbaro); // in meters 
  //Serial.print(",");
  //Serial.print(altsmooth); // exponentially smoothed
  //Serial.println("");
  Serial.print("Altitude:");
  Serial.print(altbaro); //en m
  Serial.println("");
  return(altbaro-0.3);//+0,3 pour compenser la dérive du capteur dû au one shot mode
}

float Alt_Read(){
  //Reads altitude data (if CTRL_REG1 is set to altitude mode)
  int m_altitude = IICdata[0];
  int c_altitude = IICdata[1];
  float l_altitude = (float)(IICdata[2]>>4)/16;
  return((float)((m_altitude << 8)|c_altitude) + l_altitude);
}
 
byte IIC_Read(byte regAddr){
  // This function reads one byte over I2C
  Wire.beginTransmission(SENSORADDRESS);
  Wire.write(regAddr); // Address of CTRL_REG1
  Wire.endTransmission(false); // Send data to I2C dev with option for a repeated start. Works in Arduino V1.0.1
  Wire.requestFrom(SENSORADDRESS, 1);
  return Wire.read();
}
 
void IIC_ReadData(){  //Read Altitude/Barometer and Temperature data (5 bytes)
  //This is faster than reading individual register, as the sensor automatically increments the register address,
  //so we just keep reading...
  byte i=0;
  Wire.beginTransmission(SENSORADDRESS);
  Wire.write(0x01); // Address of CTRL_REG1
  Wire.endTransmission(false);
  Wire.requestFrom(SENSORADDRESS,5); //read 5 bytes: 3 for altitude or pressure, 2 for temperature
  while(Wire.available()) IICdata[i++] = Wire.read();
}
 
void IIC_Write(byte regAddr, byte value){
  // This function writes one byto over I2C
  Wire.beginTransmission(SENSORADDRESS);
  Wire.write(regAddr);
  Wire.write(value);
  Wire.endTransmission(true);
}

/////////////////////////////////////////////////////////////////////////////////////////////////////////
                                                    /* Radio */
void send_data(float sensorvalue, int valuelength){
  String message;
  message=message+"AT+SEND=0"+","+valuelength+","+sensorvalue+"\r";
  Serial.println(message);
}
/////////////////////////////////////////////////////////////////////////////////////////////////////////

void _softRestart(){ //restart par logiciel si besoin, uniquement pour Teensy 3.x
  Serial.end();  //clears the serial monitor  if used
  SCB_AIRCR = 0x05FA0004;  //write value for restart
}

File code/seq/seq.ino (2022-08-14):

//#include <elapsedMillis.h>
#include <Servo.h>

//#define DEBUG

//#define I_JCK (23)  // signal jack
//#define O_ARM (19)  // signal armement
//#define O_VOL (21)  // signal phase vol
//#define O_EJC (20)  // signal ejection
//#define O_SRV (9)   // commande servomoteur

#define I_JCK (8)  // signal jack
#define O_ARM (4)  // signal armement
#define O_VOL (5)  // signal phase vol
#define O_EJC (6)  // signal ejection
#define O_SRV (3)  // commande servomoteur

enum {E_VEILLE, E_ARME, E_VOL, E_EJECTION};  // etats du sequenceur
uint16_t const c_ouvert(1640);         // step ouverture systeme separation (us)
uint16_t const c_ferme(1920);          // step fermeture systeme separation (us)
uint16_t const c_minTravel(800);
uint16_t const c_maxTravel(2200);
uint16_t const c_delaiAntiRebond(100);  // delai anti-rebond prise jack (ms)
uint16_t const c_delaiClignotant(1000); // led clignotante au depart
uint16_t const c_dureeVol(20500);      // duree phase vol avant ejection (ms)

bool etat_servo(LOW), etat_servo_precedent(LOW);
bool jack_precedent(HIGH), jack_courant(HIGH), jack(false);
bool clignotant(LOW);
uint8_t etat_precedent(E_VEILLE), etat(E_VEILLE);
//elapsedMillis tpsArm, tpsJck, tpsVol;

Servo grosServo;
// PWMServo grosServo;

void setup() {
  pinMode(I_JCK, INPUT_PULLUP);
  pinMode(O_ARM, OUTPUT);
  pinMode(O_VOL, OUTPUT);
  pinMode(O_EJC, OUTPUT);
  pinMode(O_SRV, OUTPUT);

  #ifdef DEBUG
    Serial.begin(115200);
    Serial.println("LISTE DES ETATS :\n0\tetat initial\n1\tetat arme\n2\tetat vol\n3\tetat ejecte");
    Serial.println("\netat\tservo\tjack\tduree vol");

    pinMode(LED_BUILTIN, OUTPUT);
    digitalWrite(LED_BUILTIN, HIGH);
  #endif

  grosServo.attach(O_SRV, c_minTravel, c_maxTravel);
  grosServo.writeMicroseconds(c_ferme);
}

void loop() {
  // for (int i(1500); i <= 1750; i += 50){
  //   delay(1000);
  //   grosServo.writeMicroseconds(i);  
  // }

  // for (int i(1750); i >= 1500; i -= 50){
  //   delay(1000);
  //   grosServo.writeMicroseconds(i);  
  // }
  // return;


  // delay(2000);
  // grosServo.writeMicroseconds(1400);
  // delay(2000);
  // grosServo.writeMicroseconds(2000);
  // return;

  #ifdef DEBUG
    Serial.print(etat); Serial.print('\t');
    Serial.print(etat_servo); Serial.print('\t');
    Serial.print(jack); Serial.print('\t');
//    Serial.print(tpsVol); Serial.print('\n');

    digitalWrite(LED_BUILTIN, jack);

    //delay(10);
  #endif

  /* bloc jack anti-rebond */
//  jack_courant = digitalRead(I_JCK);
//  if (jack_courant == jack_precedent){
//      tpsJck = 0;
//  }
//  else if (tpsJck > c_delaiAntiRebond){
//    jack = !jack_courant;
//    jack_precedent = jack_courant;
//  }

////////////////////////////////////////////////////////////////////////////////

  grosServo.writeMicroseconds(c_ferme);
  digitalWrite(O_ARM, HIGH);
  
  while (!digitalRead(I_JCK));
  digitalWrite(O_VOL, HIGH);

  delay(c_dureeVol);

  grosServo.writeMicroseconds(c_ouvert);
  digitalWrite(O_EJC, HIGH);

  while (digitalRead(I_JCK));
  digitalWrite(O_VOL, LOW);
  digitalWrite(O_EJC, LOW);

  delay(200);

  /* bloc machine a etat */
//  switch (etat){
//    case E_VEILLE:
//      if (tpsArm >= c_delaiClignotant){
//        clignotant = !clignotant;
//        tpsArm -= c_delaiClignotant;
//        digitalWrite(O_ARM, clignotant);
//      }
//      grosServo.write(0);
//      if (jack){
//        etat = E_ARME;
//        digitalWrite(O_ARM, HIGH);
//      }
//      break;
//    ////////////////////////////////////////
//    case E_ARME:
//      //grosServo.writeMicroseconds(c_ferme);
//      // grosServo.detach();
//      digitalWrite(O_ARM, HIGH);
//      digitalWrite(O_VOL, LOW);
//      digitalWrite(O_EJC, LOW);
//      if (!jack){
//        tpsVol = 0;
//        etat = E_VOL;
//        digitalWrite(O_VOL, HIGH);
//      }
//      break;
//    ////////////////////////////////////////
//    case E_VOL:
//      //grosServo.writeMicroseconds(c_ferme);
//      // grosServo.attach(O_SRV);
//      digitalWrite(O_VOL, HIGH);
//      if (tpsVol > c_dureeVol){
//        etat = E_EJECTION;
//        etat_servo = LOW;
//      }
//      break;
//    ////////////////////////////////////////
//    case E_EJECTION:
//      grosServo.writeMicroseconds(c_ouvert);
//      digitalWrite(O_EJC, HIGH);
//      etat = E_VEILLE;
//      break;
//  }
}

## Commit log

2022-05-27 ajout dossiers de travail
    [Adafruit BNO055 STEMMA QT.brd, Adafruit BNO055 STEMMA QT.sch, Adafruit BNO055.brd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]
2022-05-28 Ajout des capteurs
    [Adafruit_Ultimate_GPS.brd, odb.kicad_sch]
2022-05-28 Connexion SDA/SCL
    [odb.kicad_sch]
2022-05-28 ajout schematic module lora
2022-05-28 Ajout des footprint
2022-05-28 Ajout des footprint dans la bibliotheque
    [Adafruit Ultimate GPS.brd, Adafruit Ultimate GPS.sch]
2022-05-28 Ajouts de composants et connexions
    - molex
    - interrupteurs x2
    - module lora
    [odb.kicad_sch]
2022-05-28 complétion du schéma électrique
    [odb.kicad_sch]
2022-05-29 Mise à jour du pcb
    [odb.kicad_pcb, odb.kicad_sch]
2022-05-29 ajout des librairies teensy
    N.B. : chacun devra l'ajouter dans son gestionnaire de librairie, global de préférence
    [Teensy_4.0_Assembly.STEP, odb.kicad_sch]
2022-05-30 agencement approximatif des composants du pcb
    [odb.kicad_pcb, odb.kicad_sch]
2022-05-31 remplacement des bords Edge.Cuts par F.Silkscreen
2022-05-31 intervertion des labels de pins 4 et 5
2022-05-31 pcb en cours de tracé
    [odb.kicad_pcb, odb.kicad_sch]
2022-06-01 Ajout du plan de masse + intercom
2022-06-01 Jade's participation
    [odb.kicad_pcb]
2022-06-01 inversion de pins
2022-06-01 correction de pin répété
2022-06-01 complétion du pcb
    [odb.kicad_pcb, odb.kicad_sch]
2022-06-01 ajout de zones keepout
    [odb.kicad_pcb]
2022-06-01 modifications globales et fichiers gerber INACHEVES
    [odb-Edge_Cuts.gbr, odb-F_Cu.gbr, odb-NPTH.drl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]
2022-06-01 gerbers mis à jour
    [odb-Edge_Cuts.gbr, odb-F_Cu.gbr, odb-NPTH.drl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]
2022-06-11 code servo commandable par potentiomètre
2022-06-11 code test pour stepper
2022-06-14 Ajout du code de réception
2022-06-14 ajout d'un flag de debug
2022-06-14 Correction d'espacement + nettoyage du file system du projet
    [Adafruit BNO055 STEMMA QT.brd, Adafruit BNO055 STEMMA QT.sch, Adafruit BNO055.brd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]
2022-06-14 réorganisation des lib
    [Adafruit BNO055 STEMMA QT.brd, Adafruit BNO055 STEMMA QT.sch, Adafruit BNO055.brd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]
2022-06-15 ajout symbole BMS
2022-06-16 amélioration route sw
    [odb.kicad_pcb, odb.kicad_sch]
2022-06-16 ajout pcb séquenceur
    [seq.kicad_pcb, seq.kicad_sch]
2022-06-17 Nouveau mapping perçage + gerber
    [odb.kicad_pcb, odb.kicad_sch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]
2022-06-18 sauvetage, màj seq version à usiner
    [seq-B_Cu.gbr, seq-B_Mask.gbr, seq-B_Paste.gbr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]
2022-06-23 màj et génération des fichiers de fabrication
    les silkscreens et masks ont été ajoutés pour les les deux côtés du pcb, au cas où
    [odb-B_Cu.gbr, odb-B_Mask.gbr, odb-B_Silkscreen.gbr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]
2022-06-24 Ajout du lien du site de top aéro
2022-06-25 Pins alternatifs + suppressions des warnings
2022-06-25 Migration code sequenceur vers PlatformIO
    Note : il manque le dossier de configuration .pio (et .vscode si créé via VSCode) dans le dossier de code du sequenceur. Recréer le projet PlatformIO qui reprend le dossier pour le rendre compilable 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
2022-07-02 ajout de readme et debut de code pour sequenceur
2022-07-06 Remise en marche du code séquenceur de l'an dernier
2022-07-19 corrections éparses
    [odb.step, seq.kicad_pcb, seq.step]
2022-07-19 lutte sans merci contre le servomoteur
2022-07-21 solution partielle pio de secours incomplète et non correspondantes à la version finale
    aucun intérêt si ce n'est de conserver l'historique des modifications
2022-08-14 solution finale utilisée en vol
    [seq.kicad_sch]
2022-11-07 Ajout de documentation de fin de développement
    - édition du readme
    - réorganisations mineures de fichiers
2022-11-16 encore des erreurs d'orthographes corrigées

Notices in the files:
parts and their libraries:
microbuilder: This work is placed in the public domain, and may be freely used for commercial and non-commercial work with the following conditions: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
